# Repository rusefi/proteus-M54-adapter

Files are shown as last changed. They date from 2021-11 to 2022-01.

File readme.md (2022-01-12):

Proteus adapter for e46 non-M3 BMW

(E39 m54 should be the ms42/43 like the e46, E39 ~= E46)

https://github.com/rusefi/rusefi/wiki/BMW-e46

134 pin + Nissan board outline

https://raw.githubusercontent.com/wiki/rusefi/rusefi/OEM-Docs/Bmw/3_Series_e46/2002_bmw_325_ecu.png

https://docs.google.com/spreadsheets/d/16_VjNrk-DbMP_yDqGFelwavrGfiC9wFp73RgForjQzM

x

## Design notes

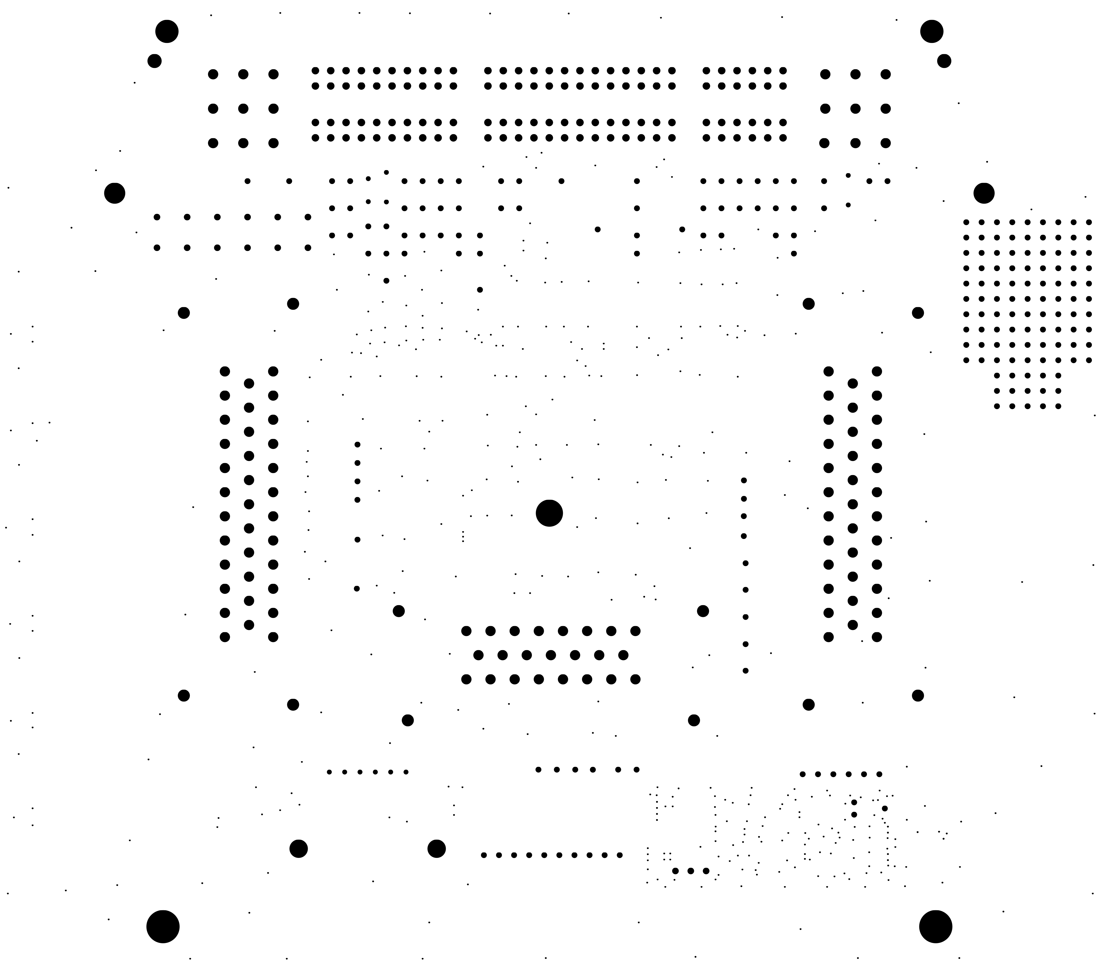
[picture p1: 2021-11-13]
proteusM54/boards/proteusM54-a/board/misc/proteusM54-a-outline.png

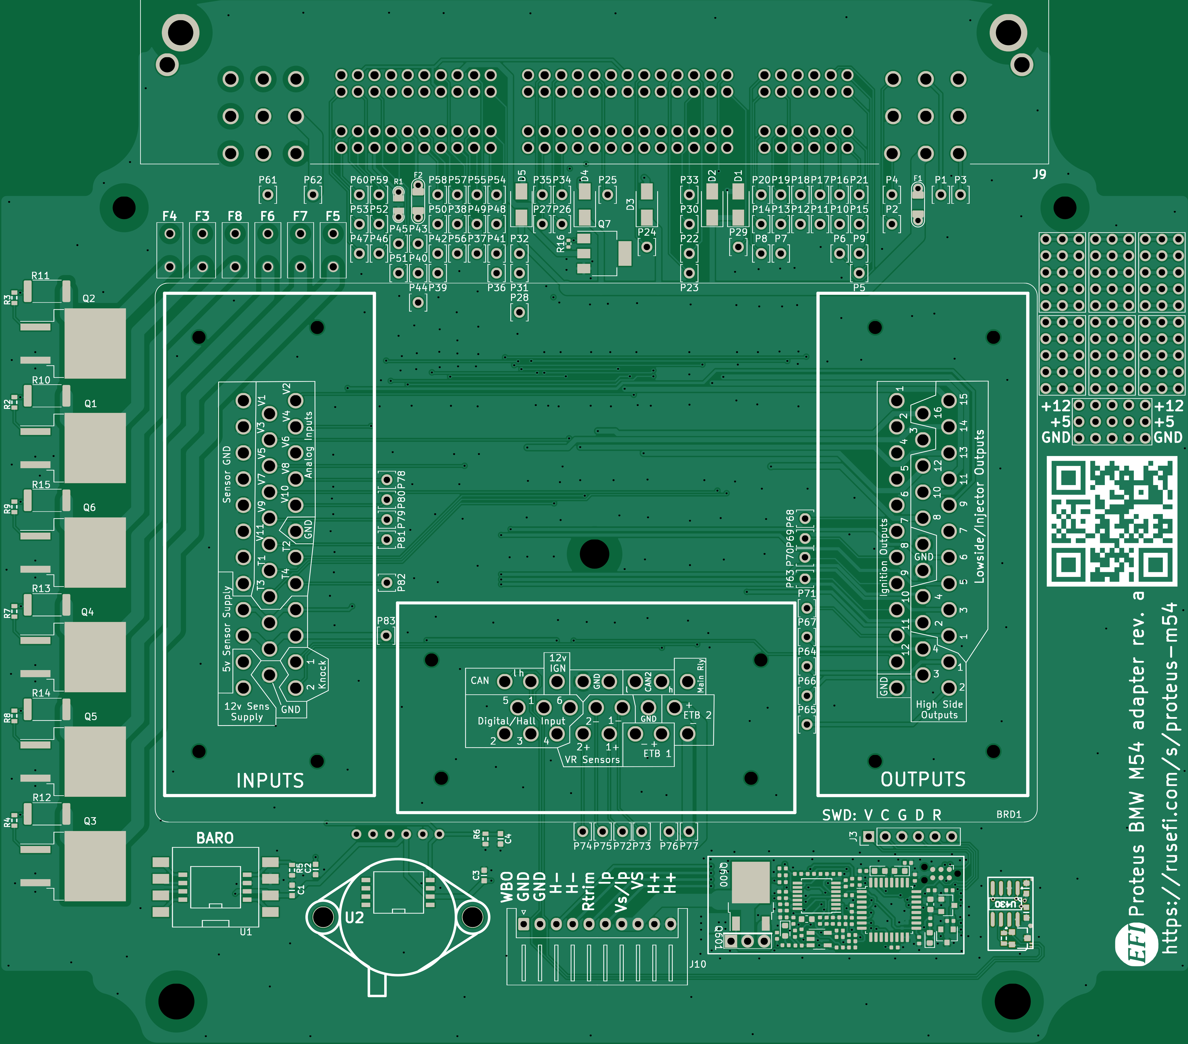
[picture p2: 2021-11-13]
proteusM54/boards/proteusM54-a/board/misc/proteusM54-a-top.png

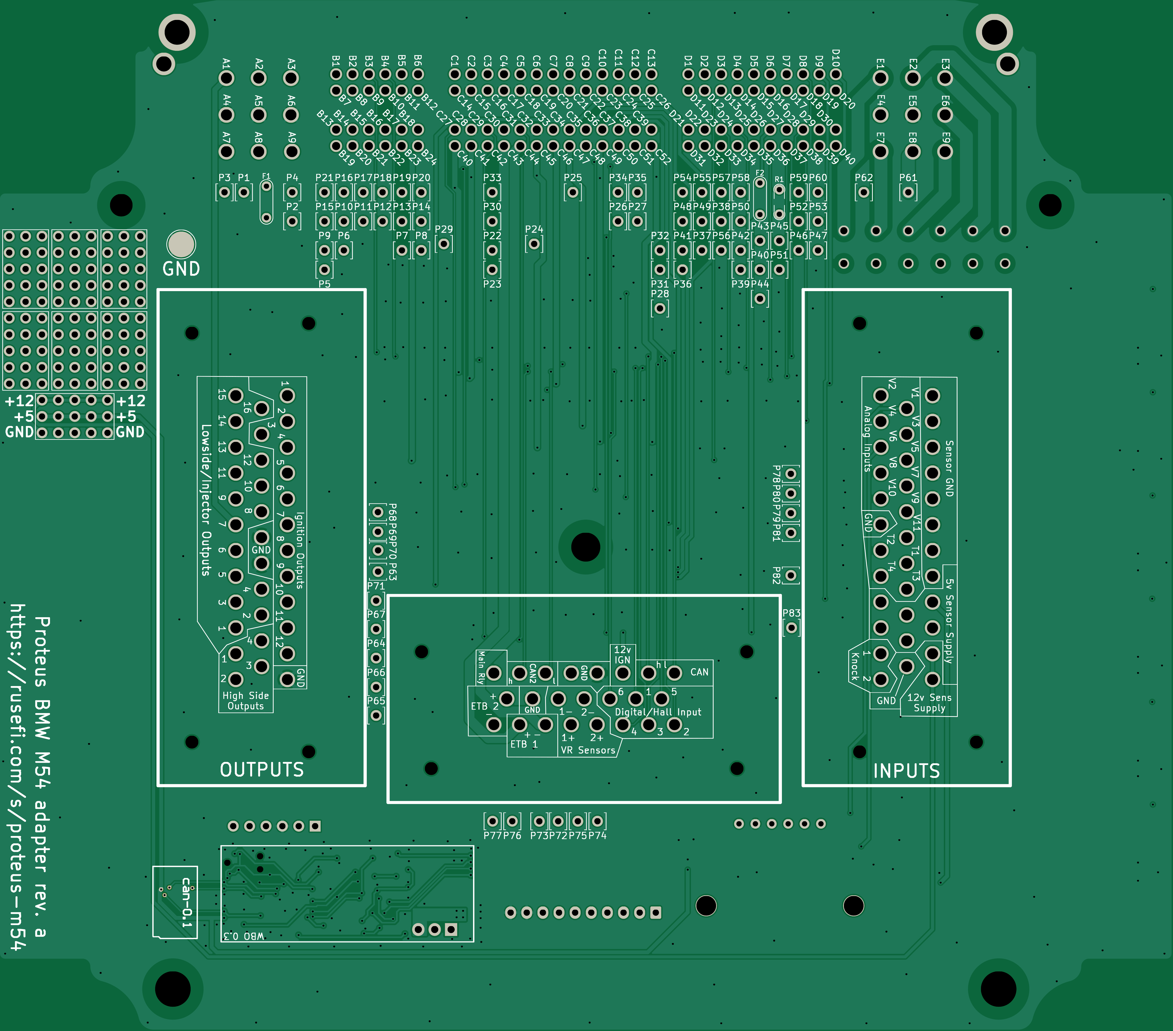
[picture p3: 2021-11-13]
proteusM54/boards/proteusM54-a/board/misc/proteusM54-a-bottom.png

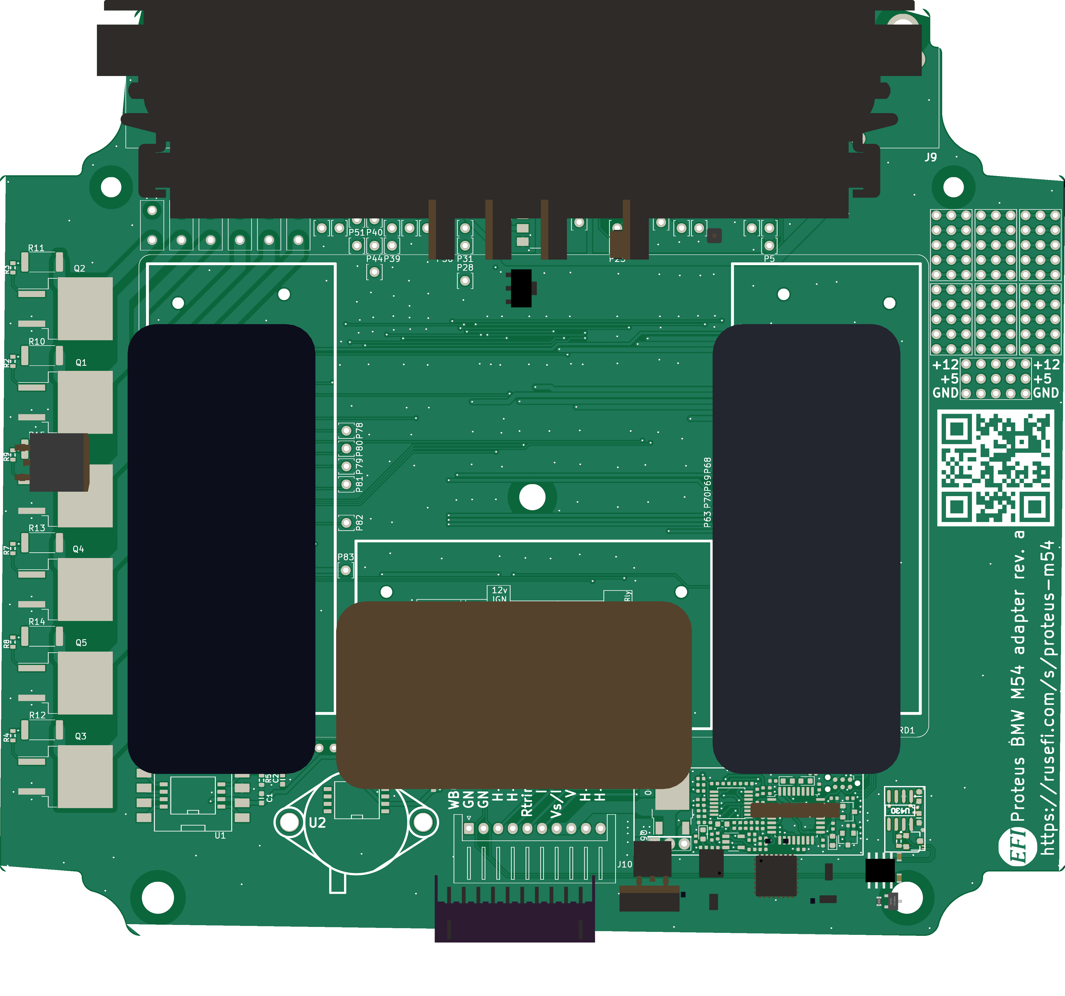
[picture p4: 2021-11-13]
proteusM54/boards/proteusM54-a/board/proteusM54-a.png

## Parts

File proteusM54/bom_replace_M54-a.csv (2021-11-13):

#WBO low-side (D2PAK | TO220)
Q600
Q601
#WBO STM32
U602
#IGN IGBT
Q1
Q2
Q3
Q4
Q5
Q6
#3.3 reference
U603 | REF3333AIDBZR | SOT-23 | C130016
#low-side
Q7 | BSP78 | SOT-223 | C56914

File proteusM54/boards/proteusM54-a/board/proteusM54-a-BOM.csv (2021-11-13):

Comment | Designator | Footprint | LCSC Part #
proteus | BRD1 | proteus
100n | C1, C3, C430, C431 | C0603 | C14663
47p | C2, C4 | C0603 | C1671
D_Schottky | D1, D2, D3, D4, D5 | D_SMA | C8678
Fuse-Pad-Pad | F1, F2 | PAD-1206-PAD | C182446
10A | F3, F4, F5, F6, F7, F8 | 36911600000 | C354908
RUSEFI_LOGO | G1 | rusefi_logo
PROTO_AREA | G2 | PROTO_AREA
PROTO_AREA | G3 | PROTO_AREA
PROTO_AREA | G4 | PROTO_AREA
PROTO_AREA | G5 | PROTO_AREA
PROTO_AREA | G6 | PROTO_AREA
PROTO_AREA | G7 | PROTO_AREA
PROTO_AREA | G8 | PROTO_AREA
Conn_01x01 | J1 | MountingHole_3.5mm
Conn_01x01 | J2 | MountingHole_3.5mm
Conn_01x06 | J3 | PinHeader_1x06_P2.54mm_Vertical
Conn_01x01 | J4 | MountingHole_5.5mm
Conn_01x01 | J5 | MountingHole_5.5mm
Conn_01x01 | J7 | TestPoint_Pad_D4.0mm
7-967288-1 | J9 | TE_7-967288-1
XH-10AW | J10 | JST_XH_S10B-XH-A_1x10_P2.50mm_Horizontal | C14652
Pad | P1 | PAD-TH
Pad | P2 | PAD-TH
Pad | P3 | PAD-TH
Pad | P4 | PAD-TH
Pad | P5 | PAD-TH
Pad | P6 | PAD-TH
Pad | P7 | PAD-TH
Pad | P8 | PAD-TH
Pad | P9 | PAD-TH
Pad | P10 | PAD-TH
Pad | P11 | PAD-TH
Pad | P12 | PAD-TH
Pad | P13 | PAD-TH
Pad | P14 | PAD-TH
Pad | P15 | PAD-TH
Pad | P16 | PAD-TH
Pad | P17 | PAD-TH
Pad | P18 | PAD-TH
Pad | P19 | PAD-TH
Pad | P20 | PAD-TH
Pad | P21 | PAD-TH
Pad | P22 | PAD-TH
Pad | P23 | PAD-TH
Pad | P24 | PAD-TH
Pad | P25 | PAD-TH
Pad | P26 | PAD-TH
Pad | P27 | PAD-TH
Pad | P28 | PAD-TH
Pad | P29 | PAD-TH
Pad | P30 | PAD-TH
Pad | P31 | PAD-TH
Pad | P32 | PAD-TH
Pad | P33 | PAD-TH
Pad | P34 | PAD-TH
Pad | P35 | PAD-TH
Pad | P36 | PAD-TH
Pad | P37 | PAD-TH
Pad | P38 | PAD-TH
Pad | P39 | PAD-TH
Pad | P40 | PAD-TH
Pad | P41 | PAD-TH
Pad | P42 | PAD-TH
Pad | P43 | PAD-TH
Pad | P44 | PAD-TH
Pad | P45 | PAD-TH
Pad | P46 | PAD-TH
Pad | P47 | PAD-TH
Pad | P48 | PAD-TH
Pad | P49 | PAD-TH
Pad | P50 | PAD-TH
Pad | P51 | PAD-TH
Pad | P52 | PAD-TH
Pad | P53 | PAD-TH
Pad | P54 | PAD-TH
Pad | P55 | PAD-TH
Pad | P56 | PAD-TH
Pad | P57 | PAD-TH
Pad | P58 | PAD-TH
Pad | P59 | PAD-TH
Pad | P60 | PAD-TH
Pad | P61 | PAD-TH
Pad | P62 | PAD-TH
Pad | P63 | PAD-TH
Pad | P64 | PAD-TH
Pad | P65 | PAD-TH
Pad | P66 | PAD-TH
Pad | P67 | PAD-TH
Pad | P68 | PAD-TH
Pad | P69 | PAD-TH
Pad | P70 | PAD-TH
Pad | P71 | PAD-TH
Pad | P72 | PAD-TH
Pad | P73 | PAD-TH
Pad | P74 | PAD-TH
Pad | P75 | PAD-TH
Pad | P76 | PAD-TH
Pad | P77 | PAD-TH
Pad | P78 | PAD-TH
Pad | P79 | PAD-TH
Pad | P80 | PAD-TH
Pad | P81 | PAD-TH
Pad | P82 | PAD-TH
Pad | P83 | PAD-TH
Jumper-Pad-Pad | R1 | PAD-0805-PAD | C17477
22 | R2, R3, R4, R7, R8, R9 | R0603 | C23345
51k | R5, R6 | R0603 | C23196
DNP | R10 | R_2512_6332Metric
DNP | R11 | R_2512_6332Metric
DNP | R12 | R_2512_6332Metric
DNP | R13 | R_2512_6332Metric
DNP | R14 | R_2512_6332Metric
DNP | R15 | R_2512_6332Metric
10k | R16 | R0402 | C60489
MPXxx6115A | U1 | MPX_SOP_SSOP
MPX4/MPXH6400_MAP | U2 | MPX-4_MAP
PESD1CAN | D430 | SOT-23 | C343993
120 | R430 | R0603 | C22787
TJA1051T/3/1J | U430 | SO8 | C38695
1u | C600, C607, C609, C610, C611 | C0402 | C52923
100n | C601, C602, C605, C608, C612, C613, C614, C615 | C0402 | C1525
33n | C603 | C0402 | C1585
DNP | C604 | C0402
DNP | C606 | C0402
4.7u | C616 | C0603 | C19666
LED-RED-0603 | D600, D603 | LED-0603 | C2286
LED-GREEN-0603 | D601 | LED-0603 | C72043
LED-BLUE-0603 | D602 | LED-0603 | C72041
1k | R600, R601, R616, R617, R622, R626, R627, R628 | R0402 | C11702
68k | R602, R603 | R0402 | C36871
10k | R604, R605, R613, R614, R618, R619, R625 | R0402 | C25744
10 | R606 | R0402 | C25077
22k | R607 | R0402 | C25768
47 | R608 | R0402 | C25118
61.9 | R609 | R0603 | C23092
20k | R610, R611, R612 | R0402 | C25765
100k | R615, R621 | R0402 | C25741
27k | R620, R623 | R0402 | C25771
3.3k | R624 | R0402 | C25890
MCP6004 | U600 | TSSOP14 | C50282
AD8628 | U601 | TSOT23-5 | C29309
XC6206P332MR | U604 | SOT-23 | C5446
REF3333AIDBZR | U603 | SOT-23 | C130016
BSP78 | Q7 | SOT-223 | C56914

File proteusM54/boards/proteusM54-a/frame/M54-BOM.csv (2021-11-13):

Comment | Designator | Footprint | LCSC Part #
proteus | BRD1 | proteus
100n | C1 | C0603 | C14663
47p | C2 | C0603 | C1671
100n | C3 | C0603 | C14663
47p | C4 | C0603 | C1671
D_Schottky | D1 | D_SMA | C8678
D_Schottky | D2 | D_SMA | C8678
D_Schottky | D3 | D_SMA | C8678
D_Schottky | D4 | D_SMA | C8678
D_Schottky | D5 | D_SMA | C8678
Fuse-Pad-Pad | F1 | PAD-1206-PAD | C182446
Fuse-Pad-Pad | F2 | PAD-1206-PAD | C182446
10A | F3 | 36911600000 | C354908
10A | F4 | 36911600000 | C354908
10A | F5 | 36911600000 | C354908
10A | F6 | 36911600000 | C354908
10A | F7 | 36911600000 | C354908
10A | F8 | 36911600000 | C354908
RUSEFI_LOGO | G1 | rusefi_logo
PROTO_AREA | G2 | PROTO_AREA
PROTO_AREA | G3 | PROTO_AREA
PROTO_AREA | G4 | PROTO_AREA
PROTO_AREA | G5 | PROTO_AREA
PROTO_AREA | G6 | PROTO_AREA
PROTO_AREA | G7 | PROTO_AREA
PROTO_AREA | G8 | PROTO_AREA
Conn_01x01 | J1 | MountingHole_3.5mm
Conn_01x01 | J2 | MountingHole_3.5mm
Conn_01x06 | J3 | PinHeader_1x06_P2.54mm_Vertical
Conn_01x01 | J4 | MountingHole_5.5mm
Conn_01x01 | J5 | MountingHole_5.5mm
Conn_01x01 | J7 | TestPoint_Pad_D4.0mm
7-967288-1 | J9 | TE_7-967288-1
XH-10AW | J10 | JST_XH_S10B-XH-A_1x10_P2.50mm_Horizontal | C14652
Module:can/0.1 | M2 | can
Module:wbo/0.3 | M3 | wbo
Pad | P1 | PAD-TH
Pad | P2 | PAD-TH
Pad | P3 | PAD-TH
Pad | P4 | PAD-TH
Pad | P5 | PAD-TH
Pad | P6 | PAD-TH
Pad | P7 | PAD-TH
Pad | P8 | PAD-TH
Pad | P9 | PAD-TH
Pad | P10 | PAD-TH
Pad | P11 | PAD-TH
Pad | P12 | PAD-TH
Pad | P13 | PAD-TH
Pad | P14 | PAD-TH
Pad | P15 | PAD-TH
Pad | P16 | PAD-TH
Pad | P17 | PAD-TH
Pad | P18 | PAD-TH
Pad | P19 | PAD-TH
Pad | P20 | PAD-TH
Pad | P21 | PAD-TH
Pad | P22 | PAD-TH
Pad | P23 | PAD-TH
Pad | P24 | PAD-TH
Pad | P25 | PAD-TH
Pad | P26 | PAD-TH
Pad | P27 | PAD-TH
Pad | P28 | PAD-TH
Pad | P29 | PAD-TH
Pad | P30 | PAD-TH
Pad | P31 | PAD-TH
Pad | P32 | PAD-TH
Pad | P33 | PAD-TH
Pad | P34 | PAD-TH
Pad | P35 | PAD-TH
Pad | P36 | PAD-TH
Pad | P37 | PAD-TH
Pad | P38 | PAD-TH
Pad | P39 | PAD-TH
Pad | P40 | PAD-TH
Pad | P41 | PAD-TH
Pad | P42 | PAD-TH
Pad | P43 | PAD-TH
Pad | P44 | PAD-TH
Pad | P45 | PAD-TH
Pad | P46 | PAD-TH
Pad | P47 | PAD-TH
Pad | P48 | PAD-TH
Pad | P49 | PAD-TH
Pad | P50 | PAD-TH
Pad | P51 | PAD-TH
Pad | P52 | PAD-TH
Pad | P53 | PAD-TH
Pad | P54 | PAD-TH
Pad | P55 | PAD-TH
Pad | P56 | PAD-TH
Pad | P57 | PAD-TH
Pad | P58 | PAD-TH
Pad | P59 | PAD-TH
Pad | P60 | PAD-TH
Pad | P61 | PAD-TH
Pad | P62 | PAD-TH
Pad | P63 | PAD-TH
Pad | P64 | PAD-TH
Pad | P65 | PAD-TH
Pad | P66 | PAD-TH
Pad | P67 | PAD-TH
Pad | P68 | PAD-TH
Pad | P69 | PAD-TH
Pad | P70 | PAD-TH
Pad | P71 | PAD-TH
Pad | P72 | PAD-TH
Pad | P73 | PAD-TH
Pad | P74 | PAD-TH
Pad | P75 | PAD-TH
Pad | P76 | PAD-TH
Pad | P77 | PAD-TH
Pad | P78 | PAD-TH
Pad | P79 | PAD-TH
Pad | P80 | PAD-TH
Pad | P81 | PAD-TH
Pad | P82 | PAD-TH
Pad | P83 | PAD-TH
ISL9V3040S3S | Q1 | TO-263-2 | C898702
ISL9V3040S3S | Q2 | TO-263-2 | C898702
ISL9V3040S3S | Q3 | TO-263-2 | C898702
ISL9V3040S3S | Q4 | TO-263-2 | C898702
ISL9V3040S3S | Q5 | TO-263-2 | C898702
ISL9V3040S3S | Q6 | TO-263-2 | C898702
AUIPS2041LTR | Q7 | SOT-223 | C113610
Jumper-Pad-Pad | R1 | PAD-0805-PAD | C17477
22 | R2 | R0603 | C23345
22 | R3 | R0603 | C23345
22 | R4 | R0603 | C23345
51k | R5 | R0603 | C23196
51k | R6 | R0603 | C23196
22 | R7 | R0603 | C23345
22 | R8 | R0603 | C23345
22 | R9 | R0603 | C23345
DNP | R10 | R_2512_6332Metric
DNP | R11 | R_2512_6332Metric
DNP | R12 | R_2512_6332Metric
DNP | R13 | R_2512_6332Metric
DNP | R14 | R_2512_6332Metric
DNP | R15 | R_2512_6332Metric
10k | R16 | R0402 | C60489
MPXxx6115A | U1 | MPX_SOP_SSOP
MPX4/MPXH6400_MAP | U2 | MPX-4_MAP

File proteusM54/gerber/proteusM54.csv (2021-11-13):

Comment | Designator | Footprint | LCSC Part #
proteus | BRD1 | kicad6-libraries:proteus
100n | C1 | hellen-one-common:C0603 | C14663
47p | C2 | hellen-one-common:C0603 | C1671
100n | C3 | hellen-one-common:C0603 | C14663
47p | C4 | hellen-one-common:C0603 | C1671
D_Schottky | D1 | Diode_SMD:D_SMA | C8678
D_Schottky | D2 | Diode_SMD:D_SMA | C8678
D_Schottky | D3 | Diode_SMD:D_SMA | C8678
D_Schottky | D4 | Diode_SMD:D_SMA | C8678
D_Schottky | D5 | Diode_SMD:D_SMA | C8678
Fuse-Pad-Pad | F1 | hellen-one-common:PAD-1206-PAD | C182446
Fuse-Pad-Pad | F2 | hellen-one-common:PAD-1206-PAD | C182446
10A | F3 | hellen-one-common:36911600000 | C354908
10A | F4 | hellen-one-common:36911600000 | C354908
10A | F5 | hellen-one-common:36911600000 | C354908
10A | F6 | hellen-one-common:36911600000 | C354908
10A | F7 | hellen-one-common:36911600000 | C354908
10A | F8 | hellen-one-common:36911600000 | C354908
RUSEFI_LOGO | G1 | kicad6-libraries:rusefi_logo
PROTO_AREA | G2 | hellen-one-common:PROTO_AREA
PROTO_AREA | G3 | hellen-one-common:PROTO_AREA
PROTO_AREA | G4 | hellen-one-common:PROTO_AREA
PROTO_AREA | G5 | hellen-one-common:PROTO_AREA
PROTO_AREA | G6 | hellen-one-common:PROTO_AREA
PROTO_AREA | G7 | hellen-one-common:PROTO_AREA
PROTO_AREA | G8 | hellen-one-common:PROTO_AREA
Conn_01x01 | J1 | MountingHole:MountingHole_3.5mm
Conn_01x01 | J2 | MountingHole:MountingHole_3.5mm
Conn_01x06 | J3 | Connector_PinHeader_2.54mm:PinHeader_1x06_P2.54mm_Vertical
Conn_01x01 | J4 | MountingHole:MountingHole_5.5mm
Conn_01x01 | J5 | MountingHole:MountingHole_5.5mm
Conn_01x01 | J7 | TestPoint:TestPoint_Pad_D4.0mm
7-967288-1 | J9 | kicad6-libraries:TE_7-967288-1
XH-10AW | J10 | Connector_JST:JST_XH_S10B-XH-A_1x10_P2.50mm_Horizontal | C14652
Module-can-0.1 | M2 | hellen-one-can-0.1:can
Module-wbo-0.3 | M3 | hellen-one-wbo-0.3:wbo
Pad | P1 | hellen-one-common:PAD-TH
Pad | P2 | hellen-one-common:PAD-TH
Pad | P3 | hellen-one-common:PAD-TH
Pad | P4 | hellen-one-common:PAD-TH
Pad | P5 | hellen-one-common:PAD-TH
Pad | P6 | hellen-one-common:PAD-TH
Pad | P7 | hellen-one-common:PAD-TH
Pad | P8 | hellen-one-common:PAD-TH
Pad | P9 | hellen-one-common:PAD-TH
Pad | P10 | hellen-one-common:PAD-TH
Pad | P11 | hellen-one-common:PAD-TH
Pad | P12 | hellen-one-common:PAD-TH
Pad | P13 | hellen-one-common:PAD-TH
Pad | P14 | hellen-one-common:PAD-TH
Pad | P15 | hellen-one-common:PAD-TH
Pad | P16 | hellen-one-common:PAD-TH
Pad | P17 | hellen-one-common:PAD-TH
Pad | P18 | hellen-one-common:PAD-TH
Pad | P19 | hellen-one-common:PAD-TH
Pad | P20 | hellen-one-common:PAD-TH
Pad | P21 | hellen-one-common:PAD-TH
Pad | P22 | hellen-one-common:PAD-TH
Pad | P23 | hellen-one-common:PAD-TH
Pad | P24 | hellen-one-common:PAD-TH
Pad | P25 | hellen-one-common:PAD-TH
Pad | P26 | hellen-one-common:PAD-TH
Pad | P27 | hellen-one-common:PAD-TH
Pad | P28 | hellen-one-common:PAD-TH
Pad | P29 | hellen-one-common:PAD-TH
Pad | P30 | hellen-one-common:PAD-TH
Pad | P31 | hellen-one-common:PAD-TH
Pad | P32 | hellen-one-common:PAD-TH
Pad | P33 | hellen-one-common:PAD-TH
Pad | P34 | hellen-one-common:PAD-TH
Pad | P35 | hellen-one-common:PAD-TH
Pad | P36 | hellen-one-common:PAD-TH
Pad | P37 | hellen-one-common:PAD-TH
Pad | P38 | hellen-one-common:PAD-TH
Pad | P39 | hellen-one-common:PAD-TH
Pad | P40 | hellen-one-common:PAD-TH
Pad | P41 | hellen-one-common:PAD-TH
Pad | P42 | hellen-one-common:PAD-TH
Pad | P43 | hellen-one-common:PAD-TH
Pad | P44 | hellen-one-common:PAD-TH
Pad | P45 | hellen-one-common:PAD-TH
Pad | P46 | hellen-one-common:PAD-TH
Pad | P47 | hellen-one-common:PAD-TH
Pad | P48 | hellen-one-common:PAD-TH
Pad | P49 | hellen-one-common:PAD-TH
Pad | P50 | hellen-one-common:PAD-TH
Pad | P51 | hellen-one-common:PAD-TH
Pad | P52 | hellen-one-common:PAD-TH
Pad | P53 | hellen-one-common:PAD-TH
Pad | P54 | hellen-one-common:PAD-TH
Pad | P55 | hellen-one-common:PAD-TH
Pad | P56 | hellen-one-common:PAD-TH
Pad | P57 | hellen-one-common:PAD-TH
Pad | P58 | hellen-one-common:PAD-TH
Pad | P59 | hellen-one-common:PAD-TH
Pad | P60 | hellen-one-common:PAD-TH
Pad | P61 | hellen-one-common:PAD-TH
Pad | P62 | hellen-one-common:PAD-TH
Pad | P63 | hellen-one-common:PAD-TH
Pad | P64 | hellen-one-common:PAD-TH
Pad | P65 | hellen-one-common:PAD-TH
Pad | P66 | hellen-one-common:PAD-TH
Pad | P67 | hellen-one-common:PAD-TH
Pad | P68 | hellen-one-common:PAD-TH
Pad | P69 | hellen-one-common:PAD-TH
Pad | P70 | hellen-one-common:PAD-TH
Pad | P71 | hellen-one-common:PAD-TH
Pad | P72 | hellen-one-common:PAD-TH
Pad | P73 | hellen-one-common:PAD-TH
Pad | P74 | hellen-one-common:PAD-TH
Pad | P75 | hellen-one-common:PAD-TH
Pad | P76 | hellen-one-common:PAD-TH
Pad | P77 | hellen-one-common:PAD-TH
Pad | P78 | hellen-one-common:PAD-TH
Pad | P79 | hellen-one-common:PAD-TH
Pad | P80 | hellen-one-common:PAD-TH
Pad | P81 | hellen-one-common:PAD-TH
Pad | P82 | hellen-one-common:PAD-TH
Pad | P83 | hellen-one-common:PAD-TH
ISL9V3040S3S | Q1 | Package_TO_SOT_SMD:TO-263-2 | C898702
ISL9V3040S3S | Q2 | Package_TO_SOT_SMD:TO-263-2 | C898702
ISL9V3040S3S | Q3 | Package_TO_SOT_SMD:TO-263-2 | C898702
ISL9V3040S3S | Q4 | Package_TO_SOT_SMD:TO-263-2 | C898702
ISL9V3040S3S | Q5 | Package_TO_SOT_SMD:TO-263-2 | C898702
ISL9V3040S3S | Q6 | Package_TO_SOT_SMD:TO-263-2 | C898702
AUIPS2041LTR | Q7 | Package_TO_SOT_SMD:SOT-223 | C113610
Jumper-Pad-Pad | R1 | hellen-one-common:PAD-0805-PAD | C17477
22 | R2 | hellen-one-common:R0603 | C23345
22 | R3 | hellen-one-common:R0603 | C23345
22 | R4 | hellen-one-common:R0603 | C23345
51k | R5 | hellen-one-common:R0603 | C23196
51k | R6 | hellen-one-common:R0603 | C23196
22 | R7 | hellen-one-common:R0603 | C23345
22 | R8 | hellen-one-common:R0603 | C23345
22 | R9 | hellen-one-common:R0603 | C23345
DNP | R10 | Resistor_SMD:R_2512_6332Metric
DNP | R11 | Resistor_SMD:R_2512_6332Metric
DNP | R12 | Resistor_SMD:R_2512_6332Metric
DNP | R13 | Resistor_SMD:R_2512_6332Metric
DNP | R14 | Resistor_SMD:R_2512_6332Metric
DNP | R15 | Resistor_SMD:R_2512_6332Metric
10k | R16 | Resistor_SMD:R_0402_1005Metric | C60489
MPXxx6115A | U1 | kicad6-libraries:MPX_SOP_SSOP
MPX4/MPXH6400_MAP | U2 | kicad6-libraries:MPX-4_MAP

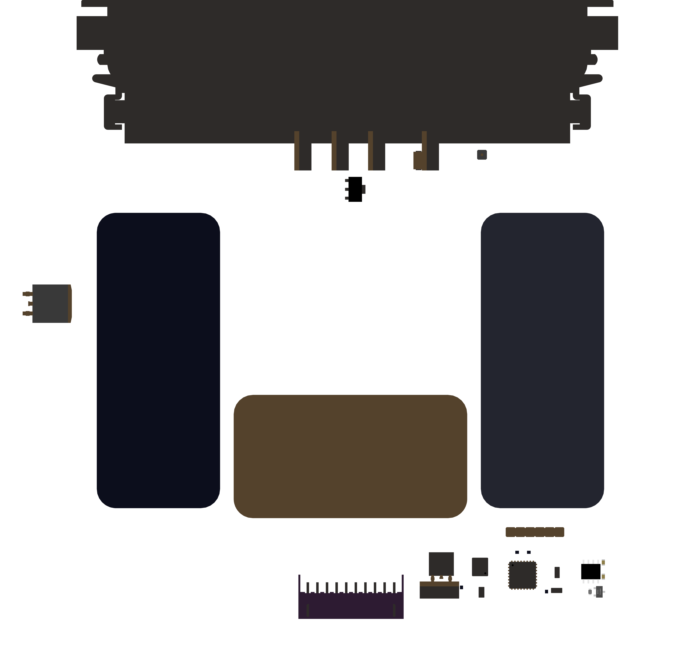
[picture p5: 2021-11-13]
proteusM54/boards/proteusM54-a/board/misc/proteusM54-a-components.png

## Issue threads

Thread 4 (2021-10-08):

Validate pinout

rusefillc, 2021-10-08:
We need to confirm that for each of the 134 pins we have connected it properly
for each pins options are

- ignore
- just a prototyping via just in case
- low side without flyback
- low side with flyback
- low current low side for relay
- low current high side
- high current high side
- analog with pull-down
- analog with pull-up
- 5v
- GND

rusefillc, 2021-10-09:
@Qwerty-OFF do you think we can have vias for all unrouted connector pins?

Qwerty-OFF, 2021-11-09:
Possibly vias for all unrouted connector pins require 4-layer board. Is it OK?
Are jumpers required for all used pins?
We don't have enough low-side pins. Can I use IGN outputs to drive MOSFETs?
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

rusefillc, 2021-11-09:
4 layers totally fine

mck1117, 2021-11-09:
>  We don't have enough low-side pins. Can I use IGN outputs to drive MOSFETs?

yes, no problem there!

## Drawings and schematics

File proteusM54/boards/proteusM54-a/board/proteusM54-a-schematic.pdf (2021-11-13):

# GND GND GND GND

P18 P16

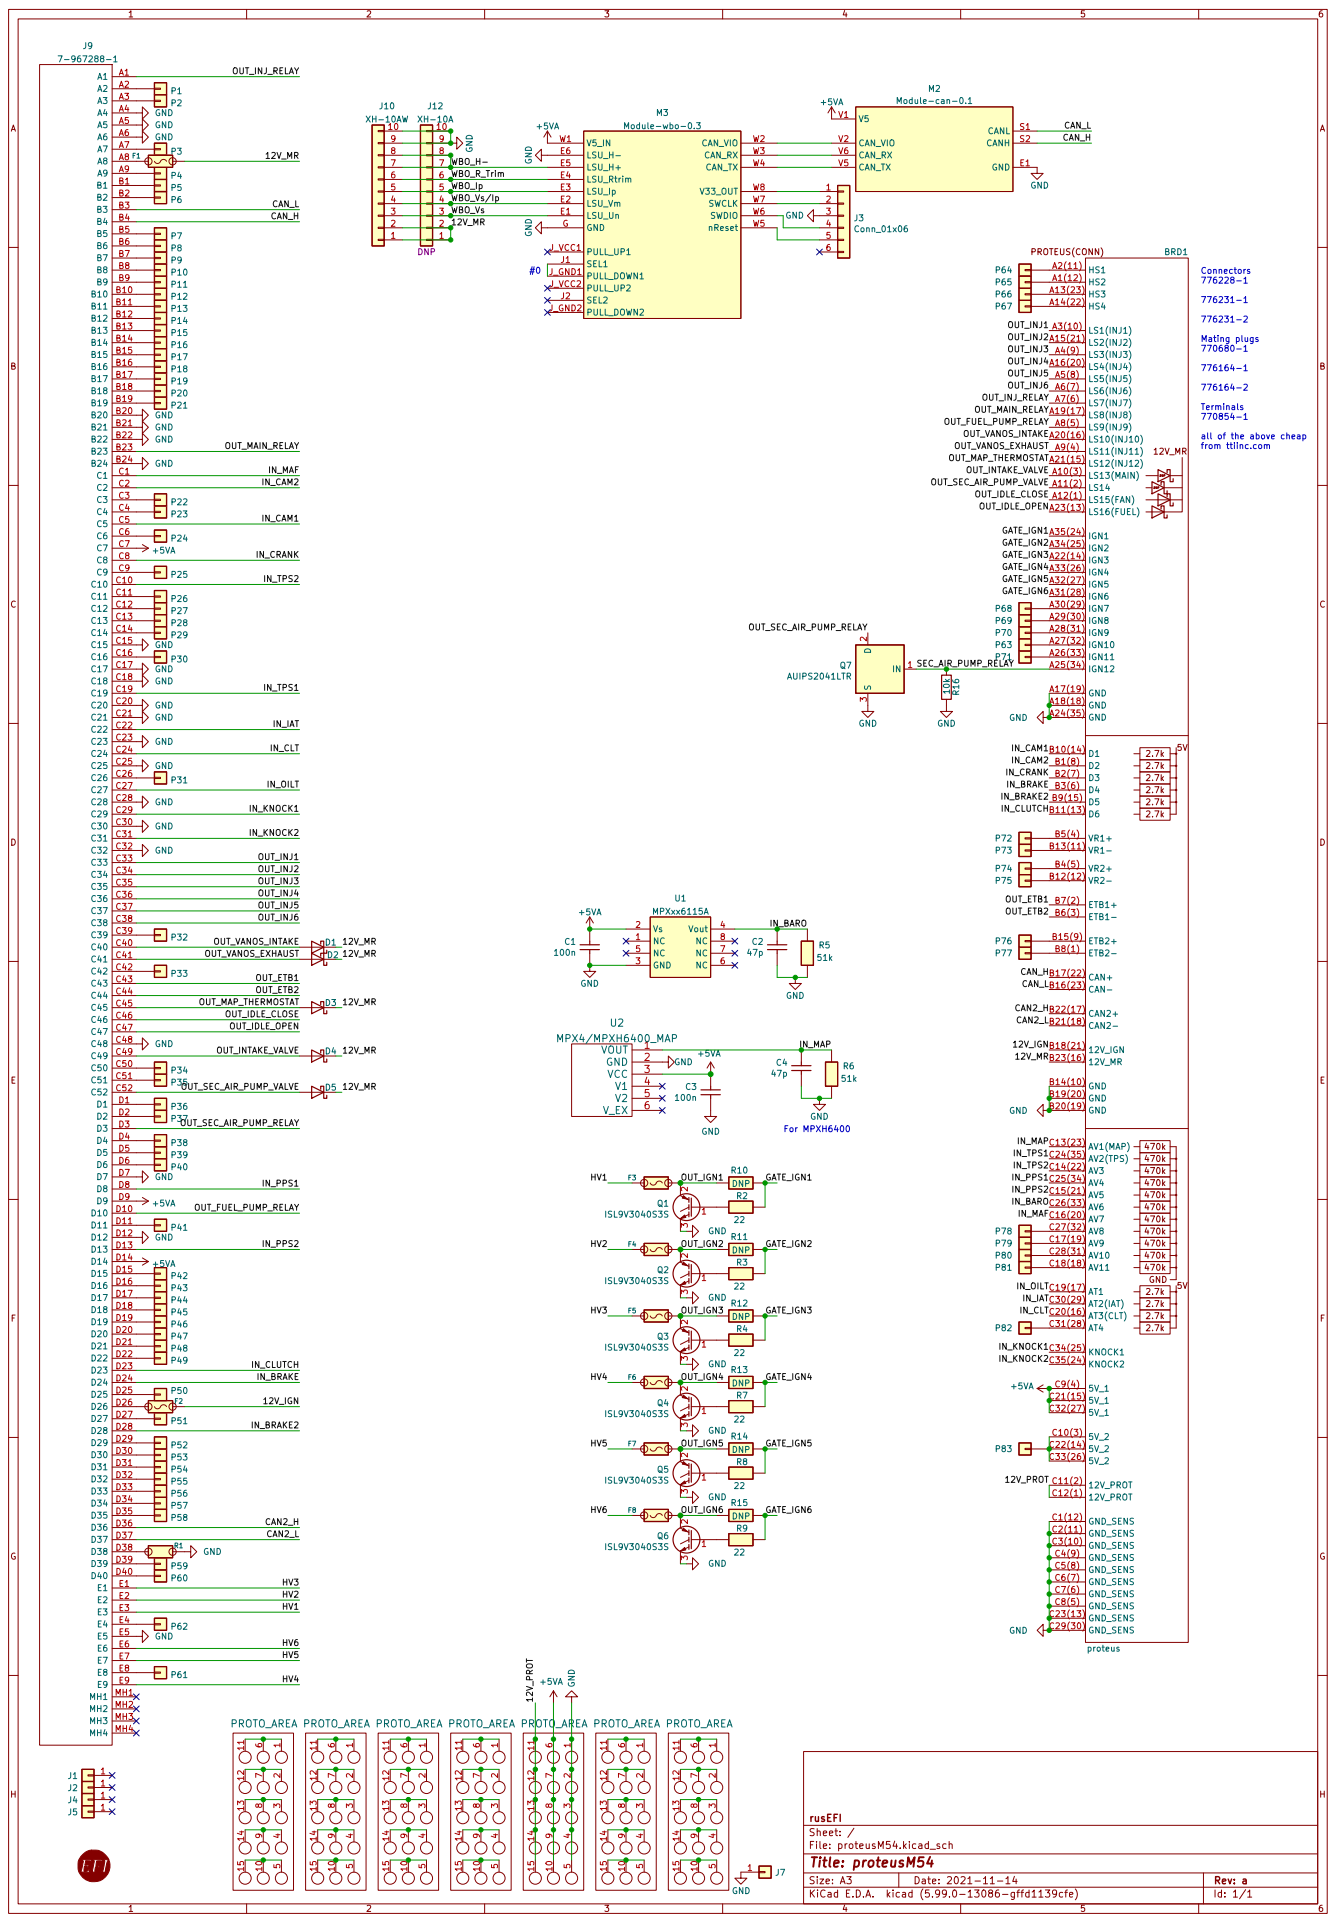
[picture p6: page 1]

all of the above cheap
from ttiinc.com

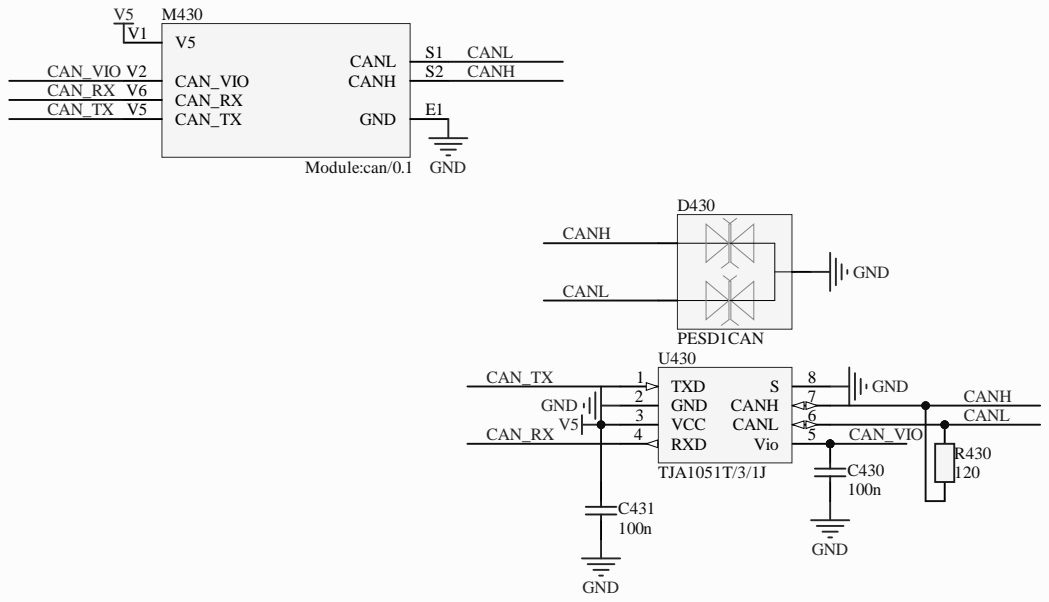
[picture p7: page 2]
andreika; Size:; Author:; Date:; Revision:; Sheet; PESD1CAN; GND; CANH; CANL; TXD 1 GND 2 VCC 3; Vio; 5 RXD 4; 6 CANH; TJA1051T/3/1J; CANH CANL; CAN_TX; CAN_RX; CAN_VIO; CAN_VIO V2; S2 CANL; CAN_TX V5; CAN_RX V6; Module:can/0.1

Hellen-One CAN
Title:

rusEFI EMS
Hellen-One Platform
https://rusefi.com/s/hellen72

1kR600

3.3k R623

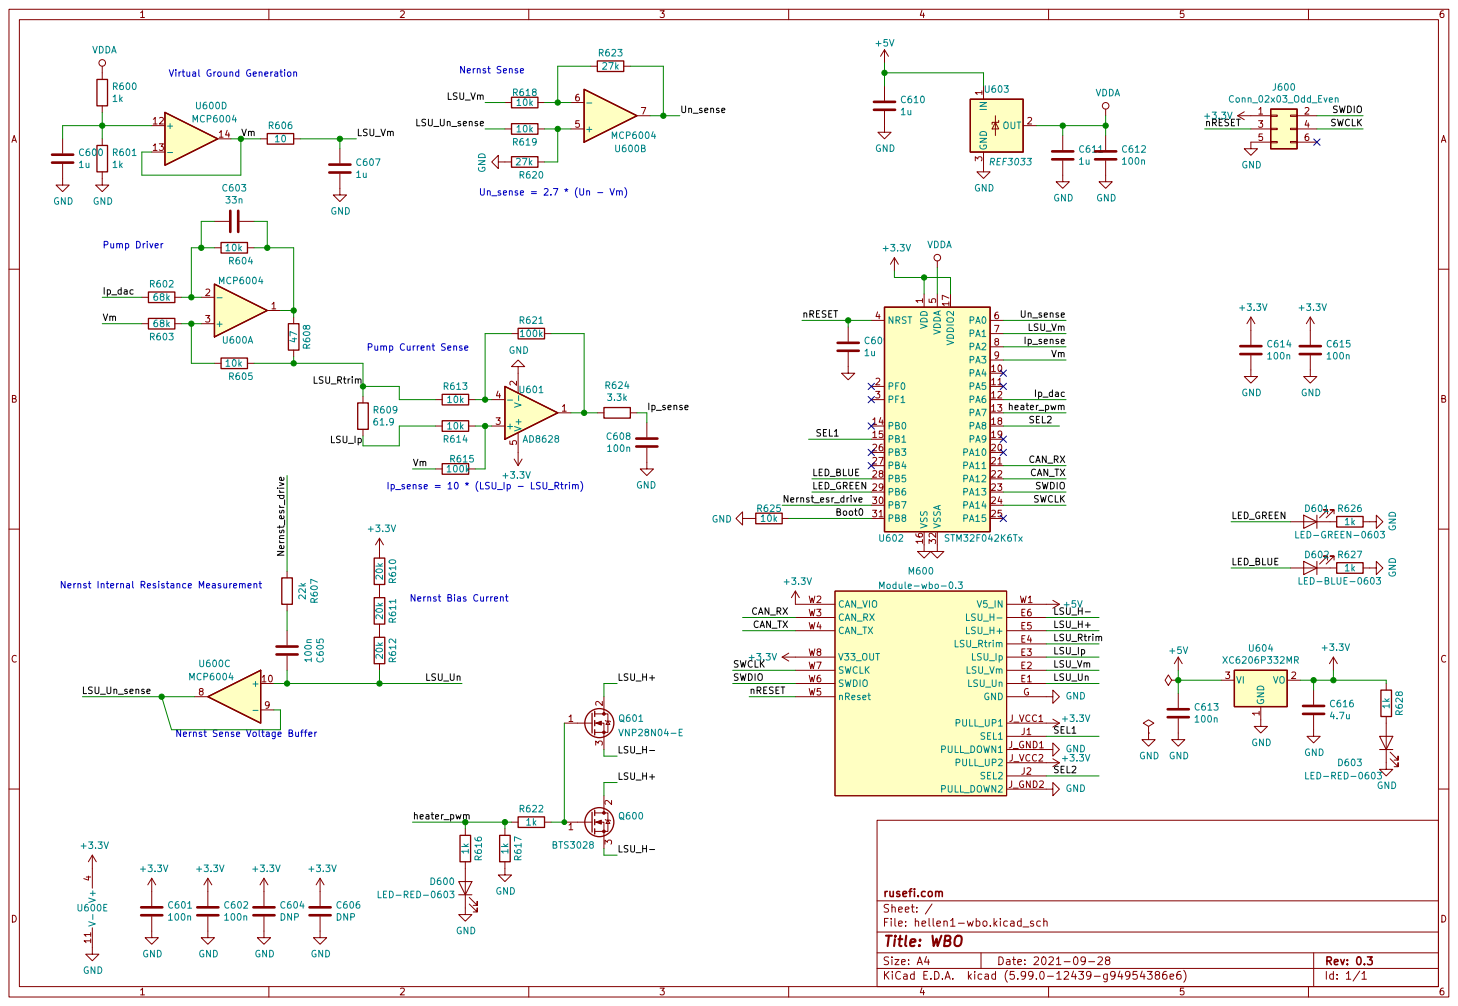
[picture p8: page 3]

Pump Current Sense Nernst Sense

LSU_Vm
Pump Driver Nernst Internal Resistance Measurement

1 VO 2 VI 3 U604 XC6206P332MR GND GND

1 PA4 10 PA5 11 PA6 12 PA7 13 PB0 14 PB1 15 VSS 16 VDDIO2 17 PA8 18 PA9 19 PF0 2 PA10 20 PA11 21 PA12 22 PA13 23 PA14 24 PA15 25 PB3 26 PB4 27 PB5 28 PB6 29 PF1 3 PB7 30 PB8 31 VSSA 32 NRST 4 VDDA

LED-RED-0603 ¹⁰⁰n C⁶⁰⁵ C604 DNP

Nernst Sense Voltage Buffer

1k GND GND R⁶¹⁶ ¹k

File: hellen1-wbo.kicad_sch Sheet: / rusefi.com

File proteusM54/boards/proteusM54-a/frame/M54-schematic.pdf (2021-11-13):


J12 XH-10A DNP GND GND GND
GND

GND GND

all of the above cheap
from ttiinc.com

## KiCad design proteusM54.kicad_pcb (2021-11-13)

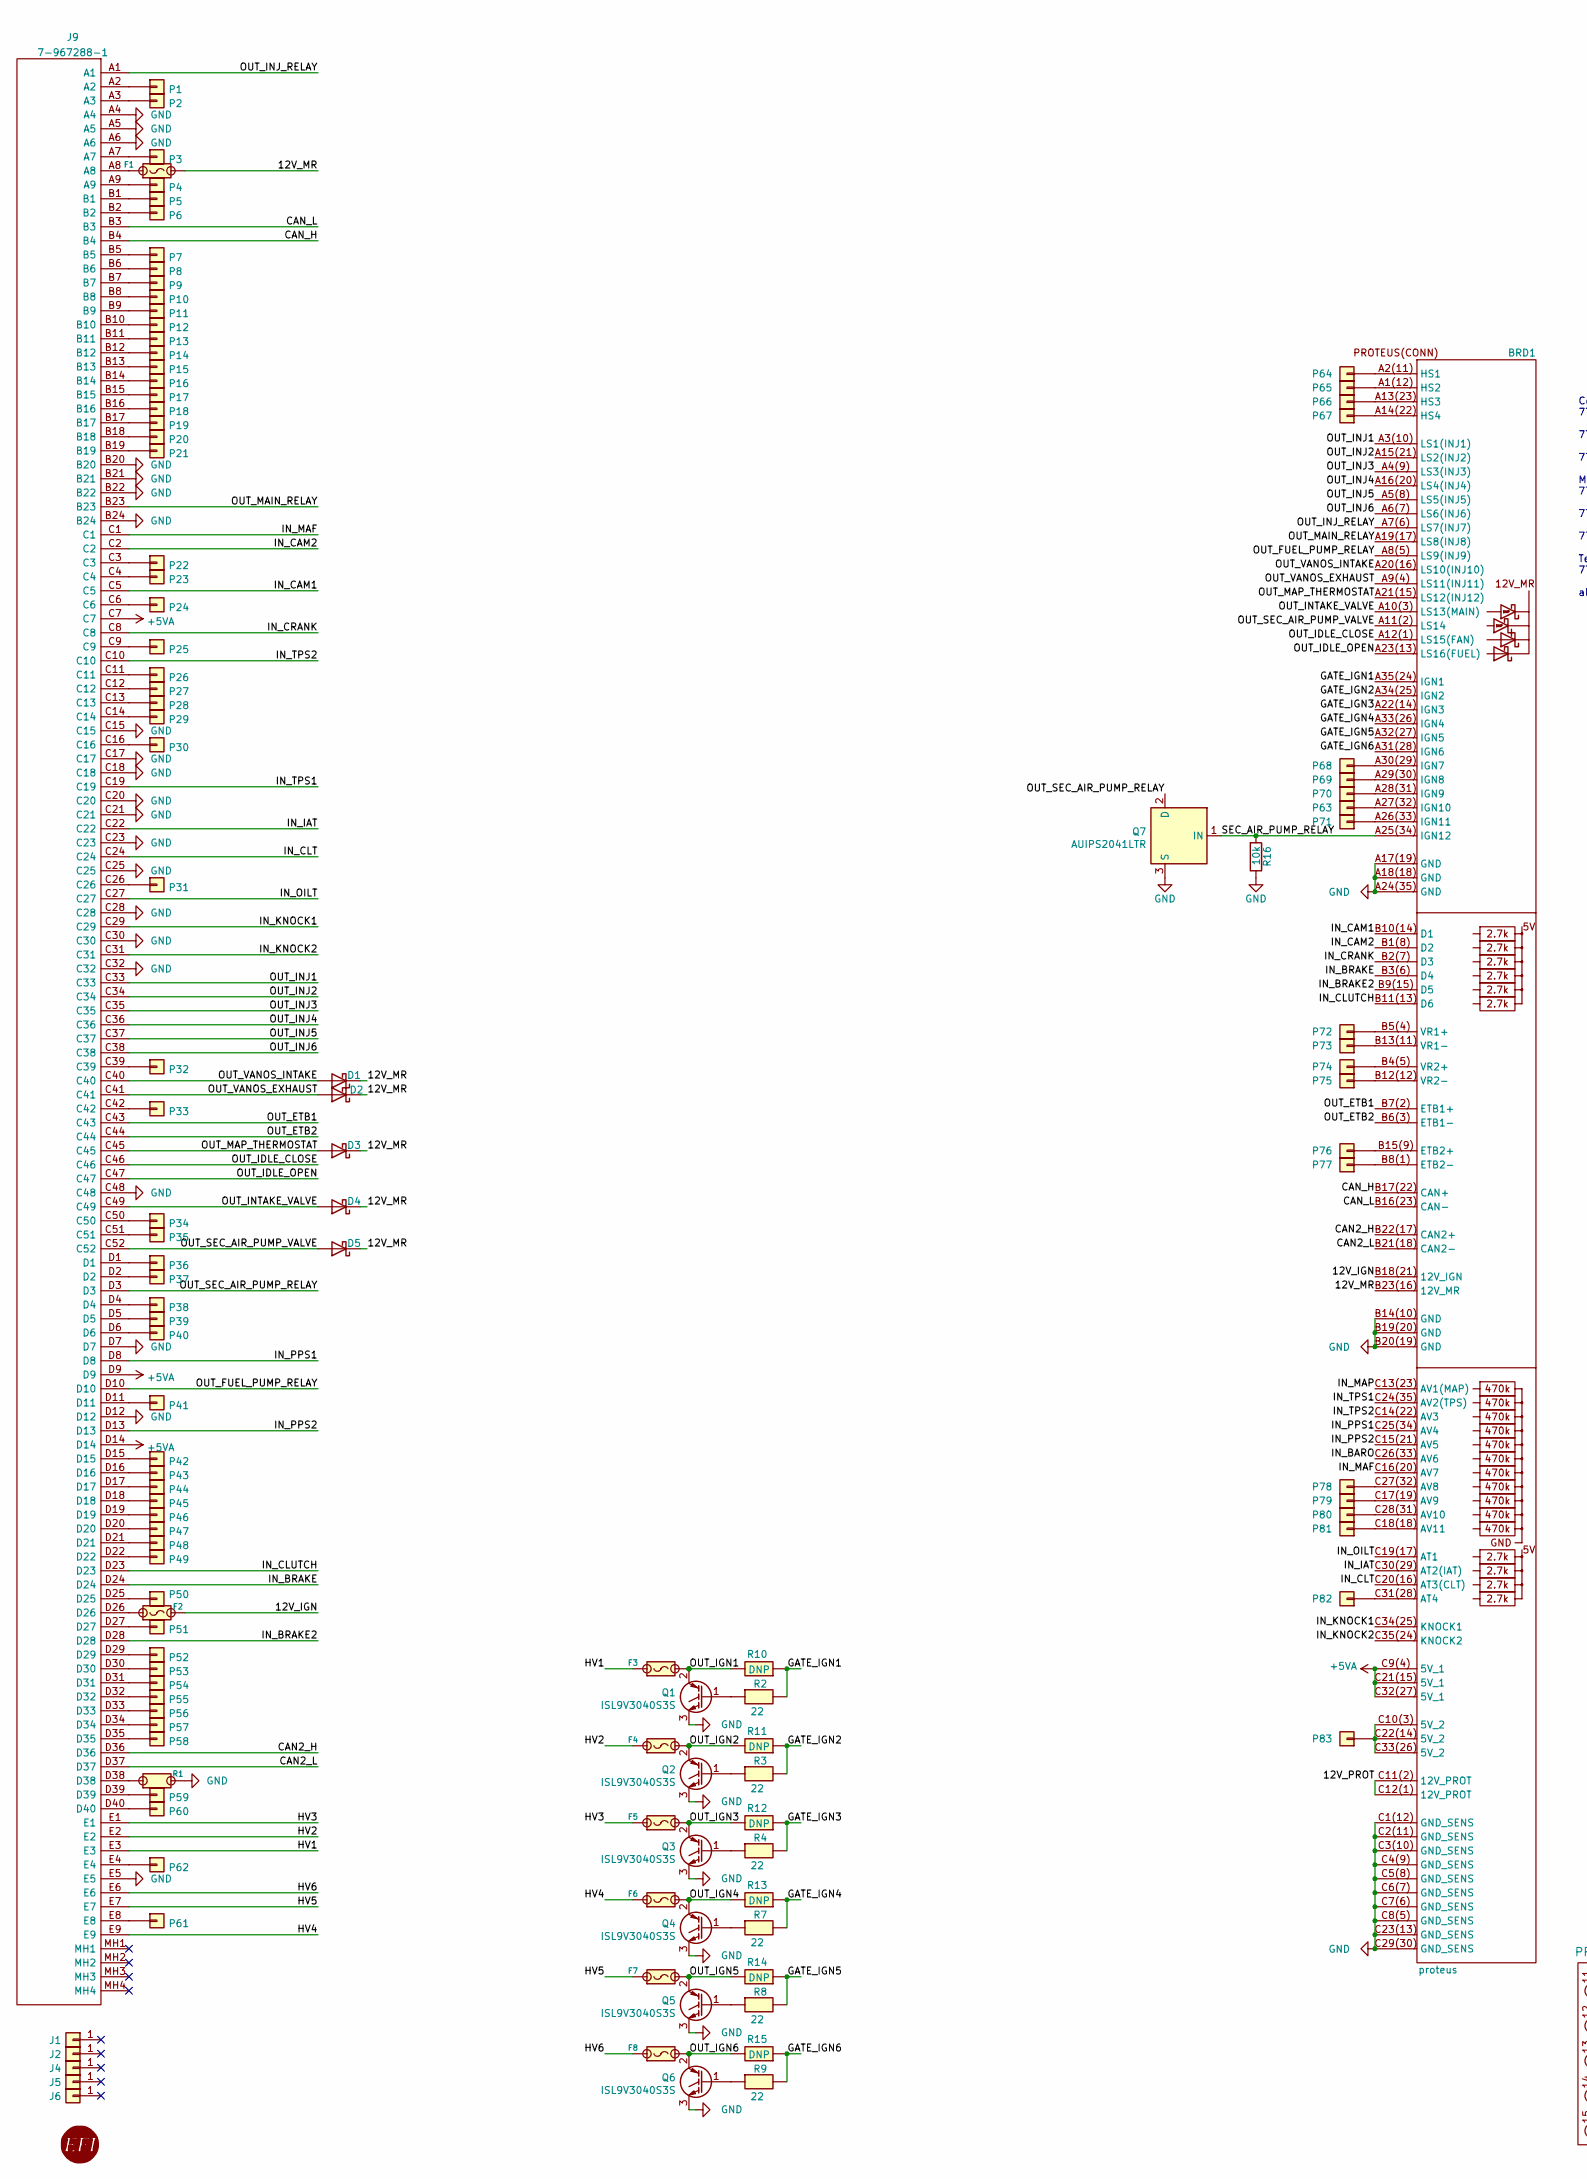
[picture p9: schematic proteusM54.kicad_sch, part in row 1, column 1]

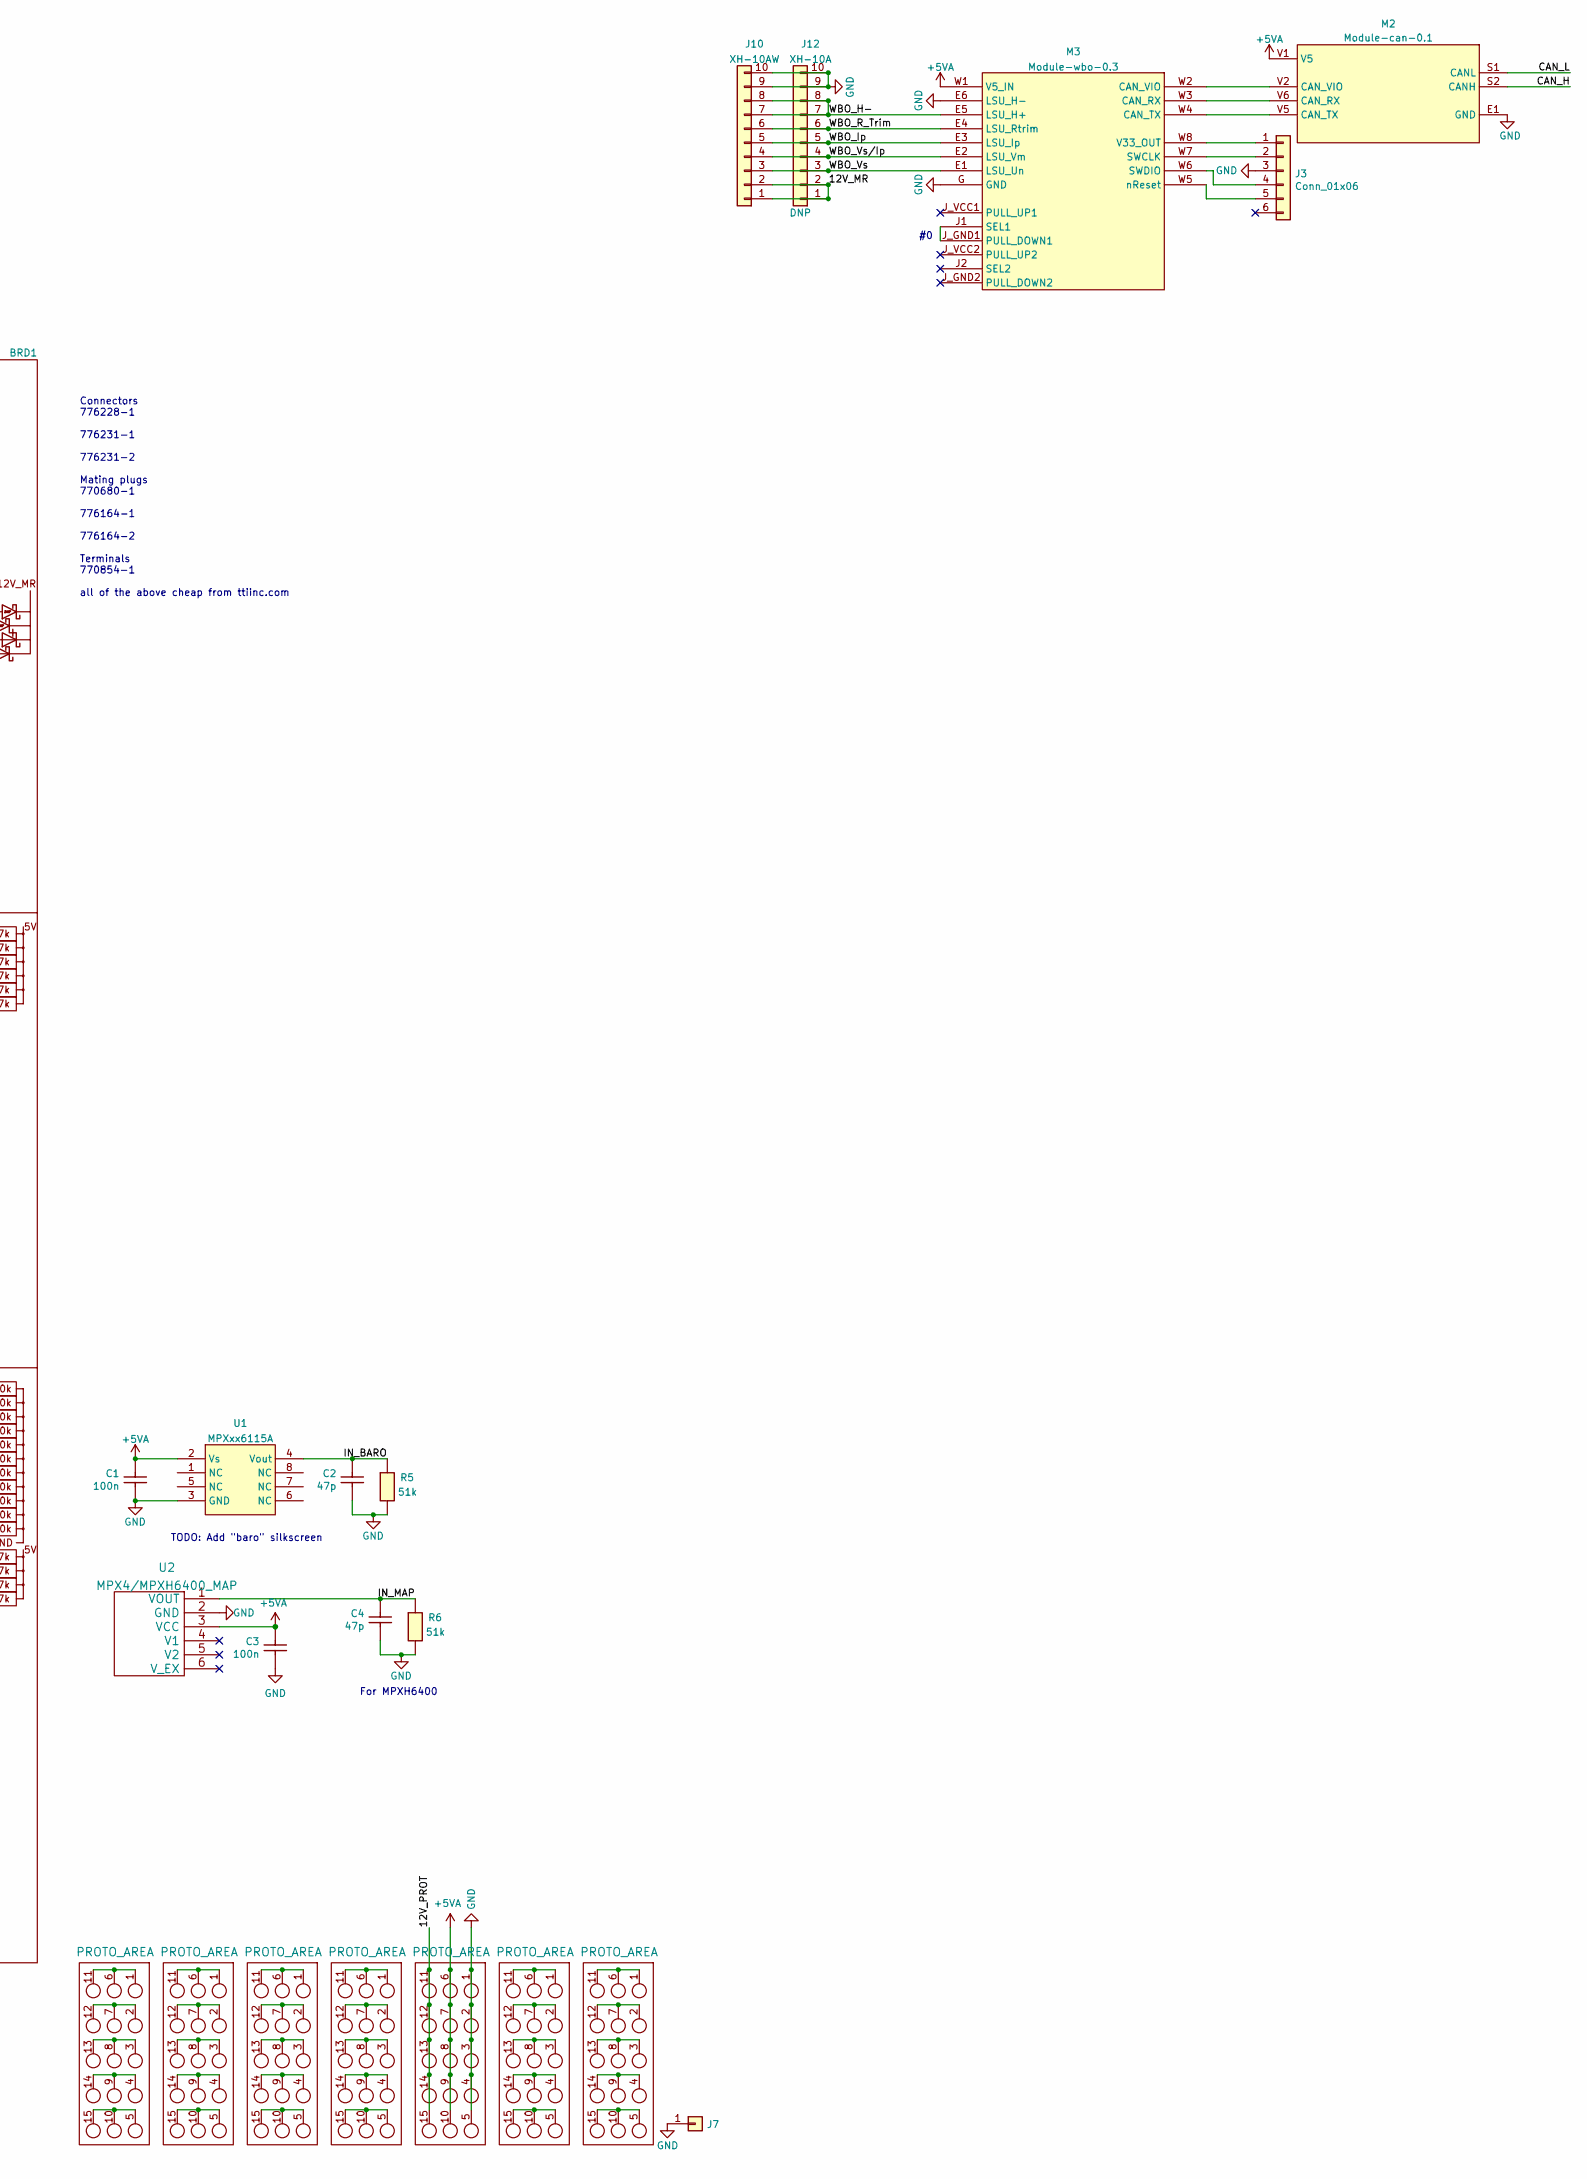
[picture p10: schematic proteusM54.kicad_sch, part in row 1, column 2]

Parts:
BRD1: proteus
C1, C3: 100n; C0603; LCSC C14663
C2, C4: 47p; C0603; LCSC C1671
D1, D2, D3, D4, D5: D_Schottky; D_SMA; LCSC C8678
F1, F2: Fuse-Pad-Pad; PAD-1206-PAD; LCSC C182446
F3, F4, F5, F6, F7, F8: 10A; 36911600000; LCSC C354908
G1: RUSEFI_LOGO; rusefi_logo
G2, G3, G4, G5, G6, G7, G8: PROTO_AREA
J1, J2: Conn_01x01; MountingHole_3.5mm
J3: Conn_01x06; PinHeader_1x06_P2.54mm_Vertical
J4, J5: Conn_01x01; MountingHole_5.5mm
J6: Conn_01x01; MountingHole_4.5mm
J7: Conn_01x01; TestPoint_Pad_D4.0mm
J9: 7-967288-1; TE_7-967288-1; Mouser Part Number 571-7-967288-1
J10: XH-10AW; JST_XH_S10B-XH-A_1x10_P2.50mm_Horizontal; LCSC C14652
J12: XH-10A; JST_XH_B10B-XH-A_1x10_P2.50mm_Vertical; LCSC C8885
M2: Module-can-0.1; can
M3: Module-wbo-0.3; wbo
P1, P2, P3, P4, P5, P6, P7, P8, P9, P10, P11, P12, P13, P14, P15, P16, P17, P18, P19, P20, P21, P22, P23, P24, P25, P26, P27, P28, P29, P30, P31, P32, P33, P34, P35, P36, P37, P38, P39, P40, P41, P42, P43, P44, P45, P46, P47, P48, P49, P50, P51, P52, P53, P54, P55, P56, P57, P58, P59, P60, P61, P62, P63, P64, P65, P66, P67, P68, P69, P70, P71, P72, P73, P74, P75, P76, P77, P78, P79, P80, P81, P82, P83: Pad; PAD-TH
Q1, Q2, Q3, Q4, Q5, Q6: ISL9V3040S3S; TO-263-2; LCSC C898702
Q7: AUIPS2041LTR; SOT-223; LCSC C113610
R1: Jumper-Pad-Pad; PAD-0805-PAD; LCSC C17477
R2, R3, R4, R7, R8, R9: 22; R0603; LCSC C23345
R5, R6: 51k; R0603; LCSC C23196
R10, R11, R12, R13, R14, R15: DNP; R_2512_6332Metric
R16: 10k; R_0402_1005Metric; LCSC C60489
U1: MPXxx6115A; MPX_SOP_SSOP
U2: MPX4/MPXH6400_MAP; MPX-4_MAP

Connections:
+5VA: BRD1.C9(4) (5V_1), BRD1.C21(15) (5V_1), BRD1.C32(27) (5V_1), C1.2, C3.2, G6.6, G6.7, G6.8, G6.9, G6.10, J9.C7, J9.D9, J9.D14, M2.V1 (V5), M3.W1 (V5_IN), U1.2 (Vs), U2.3 (VCC)
/12V_IGN: BRD1.B18(21) (12V_IGN), F2.2
/12V_MR: BRD1.B23(16) (12V_MR), D1.1 (K), D2.1 (K), D3.1 (K), D4.1 (K), D5.1 (K), F1.2, J10.1, J10.2, J12.1, J12.2
/12V_PROT: BRD1.C11(2) (12V_PROT), BRD1.C12(1) (12V_PROT), G6.11, G6.12, G6.13, G6.14, G6.15
/CAN2_H: BRD1.B22(17) (CAN2+), J9.D36
/CAN2_L: BRD1.B21(18) (CAN2-), J9.D37
/CAN_H: BRD1.B17(22) (CAN+), J9.B4, M2.S2 (CANH)
/CAN_L: BRD1.B16(23) (CAN-), J9.B3, M2.S1 (CANL)
/GATE_IGN1: BRD1.A35(24) (IGN1), R2.2, R10.1
/GATE_IGN2: BRD1.A34(25) (IGN2), R3.2, R11.1
/GATE_IGN3: BRD1.A22(14) (IGN3), R4.2, R12.1
/GATE_IGN4: BRD1.A33(26) (IGN4), R7.2, R13.1
/GATE_IGN5: BRD1.A32(27) (IGN5), R8.2, R14.1
/GATE_IGN6: BRD1.A31(28) (IGN6), R9.2, R15.1
/HV1: F3.1, J9.E3
/HV2: F4.1, J9.E2
/HV3: F5.1, J9.E1
/HV4: F6.1, J9.E9
/HV5: F7.1, J9.E7
/HV6: F8.1, J9.E6
/IN_BARO: BRD1.C26(33) (AV6), C2.2, R5.1, U1.4 (Vout)
/IN_BRAKE: BRD1.B3(6) (D4), J9.D24
/IN_BRAKE2: BRD1.B9(15) (D5), J9.D28
/IN_CAM1: BRD1.B10(14) (D1), J9.C5
/IN_CAM2: BRD1.B1(8) (D2), J9.C2
/IN_CLT: BRD1.C20(16) (AT3(CLT)), J9.C24
/IN_CLUTCH: BRD1.B11(13) (D6), J9.D23
/IN_CRANK: BRD1.B2(7) (D3), J9.C8
/IN_IAT: BRD1.C30(29) (AT2(IAT)), J9.C22
/IN_KNOCK1: BRD1.C34(25) (KNOCK1), J9.C29
/IN_KNOCK2: BRD1.C35(24) (KNOCK2), J9.C31
/IN_MAF: BRD1.C16(20) (AV7), J9.C1
/IN_MAP: BRD1.C13(23) (AV1(MAP)), C4.2, R6.1, U2.1 (VOUT)
/IN_OILT: BRD1.C19(17) (AT1), J9.C27
/IN_PPS1: BRD1.C25(34) (AV4), J9.D8
/IN_PPS2: BRD1.C15(21) (AV5), J9.D13
/IN_TPS1: BRD1.C24(35) (AV2(TPS)), J9.C19
/IN_TPS2: BRD1.C14(22) (AV3), J9.C10
/OUT_ETB1: BRD1.B7(2) (ETB1+), J9.C43
/OUT_ETB2: BRD1.B6(3) (ETB1-), J9.C44
/OUT_FUEL_PUMP_RELAY: BRD1.A8(5) (LS9(INJ9)), J9.D10
/OUT_IDLE_CLOSE: BRD1.A12(1) (LS15(FAN)), J9.C46
/OUT_IDLE_OPEN: BRD1.A23(13) (LS16(FUEL)), J9.C47
/OUT_IGN1: F3.2, Q1.2 (C), R10.2
/OUT_IGN2: F4.2, Q2.2 (C), R11.2
/OUT_IGN3: F5.2, Q3.2 (C), R12.2
/OUT_IGN4: F6.2, Q4.2 (C), R13.2
/OUT_IGN5: F7.2, Q5.2 (C), R14.2
/OUT_IGN6: F8.2, Q6.2 (C), R15.2
/OUT_INJ1: BRD1.A3(10) (LS1(INJ1)), J9.C33
/OUT_INJ2: BRD1.A15(21) (LS2(INJ2)), J9.C34
/OUT_INJ3: BRD1.A4(9) (LS3(INJ3)), J9.C35
/OUT_INJ4: BRD1.A16(20) (LS4(INJ4)), J9.C36
/OUT_INJ5: BRD1.A5(8) (LS5(INJ5)), J9.C37
/OUT_INJ6: BRD1.A6(7) (LS6(INJ6)), J9.C38
/OUT_INJ_RELAY: BRD1.A7(6) (LS7(INJ7)), J9.A1
/OUT_INTAKE_VALVE: BRD1.A10(3) (LS13(MAIN)), D4.2 (A), J9.C49
/OUT_MAIN_RELAY: BRD1.A19(17) (LS8(INJ8)), J9.B23
/OUT_MAP_THERMOSTAT: BRD1.A21(15) (LS12(INJ12)), D3.2 (A), J9.C45
/OUT_SEC_AIR_PUMP_RELAY: J9.D3, Q7.2 (D)
/OUT_SEC_AIR_PUMP_VALVE: BRD1.A11(2) (LS14), D5.2 (A), J9.C52
/OUT_VANOS_EXHAUST: BRD1.A9(4) (LS11(INJ11)), D2.2 (A), J9.C41
/OUT_VANOS_INTAKE: BRD1.A20(16) (LS10(INJ10)), D1.2 (A), J9.C40
/SEC_AIR_PUMP_RELAY: BRD1.A25(34) (IGN12), Q7.1 (IN), R16.2
/WBO_H-: J10.7, J10.8, J12.7, J12.8, M3.E5 (LSU_H+)
/WBO_Ip: J10.5, J12.5, M3.E3 (LSU_Ip)
/WBO_R_Trim: J10.6, J12.6, M3.E4 (LSU_Rtrim)
/WBO_Vs: J10.3, J12.3, M3.E1 (LSU_Un)
/WBO_Vs/Ip: J10.4, J12.4, M3.E2 (LSU_Vm)
GND: BRD1.A17(19) (GND), BRD1.A18(18) (GND), BRD1.A24(35) (GND), BRD1.B14(10) (GND), BRD1.B19(20) (GND), BRD1.B20(19) (GND), BRD1.C1(12) (GND_SENS), BRD1.C2(11) (GND_SENS), BRD1.C3(10) (GND_SENS), BRD1.C4(9) (GND_SENS), BRD1.C5(8) (GND_SENS), BRD1.C6(7) (GND_SENS), BRD1.C7(6) (GND_SENS), BRD1.C8(5) (GND_SENS), BRD1.C23(13) (GND_SENS), BRD1.C29(30) (GND_SENS), C1.1, C2.1, C3.1, C4.1, G6.1, G6.2, G6.3, G6.4, G6.5, J3.3, J7.1, J9.A4, J9.A5, J9.A6, J9.B20, J9.B21, J9.B22, J9.B24, J9.C15, J9.C17, J9.C18, J9.C20, J9.C21, J9.C23, J9.C25, J9.C28, J9.C30, J9.C32, J9.C48, J9.D7, J9.D12, J9.E5, J10.9, J10.10, J12.9, J12.10, M2.E1 (GND), M3.E6 (LSU_H-), M3.G (GND), Q1.3 (E), Q2.3 (E), Q3.3 (E), Q4.3 (E), Q5.3 (E), Q6.3 (E), Q7.3 (S), R1.2, R5.2, R6.2, R16.1, U1.3 (GND), U2.2 (GND)
unnamed: BRD1.A1(12) (HS2), P65.1
unnamed: BRD1.A2(11) (HS1), P64.1
unnamed: BRD1.A13(23) (HS3), P66.1
unnamed: BRD1.A14(22) (HS4), P67.1
unnamed: BRD1.A26(33) (IGN11), P71.1
unnamed: BRD1.A28(31) (IGN9), P70.1
unnamed: BRD1.A29(30) (IGN8), P69.1
unnamed: BRD1.A30(29) (IGN7), P68.1
unnamed: BRD1.B4(5) (VR2+), P74.1
unnamed: BRD1.B5(4) (VR1+), P72.1
unnamed: BRD1.B8(1) (ETB2-), P77.1
unnamed: BRD1.B12(12) (VR2-), P75.1
unnamed: BRD1.B13(11) (VR1-), P73.1
unnamed: BRD1.B15(9) (ETB2+), P76.1
unnamed: BRD1.C17(19) (AV9), P79.1
unnamed: BRD1.C18(18) (AV11), P81.1
unnamed: BRD1.C10(3) (5V_2), BRD1.C22(14) (5V_2), BRD1.C33(26) (5V_2), P83.1
unnamed: BRD1.C27(32) (AV8), P78.1
unnamed: BRD1.C28(31) (AV10), P80.1
unnamed: BRD1.C31(28) (AT4), P82.1
unnamed: F1.1, J9.A8
unnamed: F2.1, J9.D26
unnamed: G2.1, G2.6, G2.11
unnamed: G2.5, G2.10, G2.15
unnamed: G2.2, G2.7, G2.12
unnamed: G2.3, G2.8, G2.13
unnamed: G2.4, G2.9, G2.14
unnamed: G3.1, G3.6, G3.11
unnamed: G3.5, G3.10, G3.15
unnamed: G3.2, G3.7, G3.12
unnamed: G3.3, G3.8, G3.13
unnamed: G3.4, G3.9, G3.14
unnamed: G4.1, G4.6, G4.11
unnamed: G4.5, G4.10, G4.15
unnamed: G4.2, G4.7, G4.12
unnamed: G4.3, G4.8, G4.13
unnamed: G4.4, G4.9, G4.14
unnamed: G5.1, G5.6, G5.11
unnamed: G5.5, G5.10, G5.15
unnamed: G5.2, G5.7, G5.12
unnamed: G5.3, G5.8, G5.13
unnamed: G5.4, G5.9, G5.14
unnamed: G7.1, G7.6, G7.11
unnamed: G7.5, G7.10, G7.15
unnamed: G7.2, G7.7, G7.12
unnamed: G7.3, G7.8, G7.13
unnamed: G7.4, G7.9, G7.14
unnamed: G8.1, G8.6, G8.11
unnamed: G8.5, G8.10, G8.15
unnamed: G8.2, G8.7, G8.12
unnamed: G8.3, G8.8, G8.13
unnamed: G8.4, G8.9, G8.14
unnamed: J3.1, M3.W8 (V33_OUT)
unnamed: J3.2, M3.W7 (SWCLK)
unnamed: J3.4, M3.W6 (SWDIO)
unnamed: J3.5, M3.W5 (nReset)
unnamed: J9.A2, P1.1
unnamed: J9.A3, P2.1
unnamed: J9.A7, P3.1
unnamed: J9.A9, P4.1
unnamed: J9.B1, P5.1
unnamed: J9.B2, P6.1
unnamed: J9.B5, P7.1
unnamed: J9.B6, P8.1
unnamed: J9.B7, P9.1
unnamed: J9.B8, P10.1
unnamed: J9.B9, P11.1
unnamed: J9.B10, P12.1
unnamed: J9.B11, P13.1
unnamed: J9.B12, P14.1
unnamed: J9.B13, P15.1
unnamed: J9.B14, P16.1
unnamed: J9.B15, P17.1
unnamed: J9.B16, P18.1
unnamed: J9.B17, P19.1
unnamed: J9.B18, P20.1
unnamed: J9.B19, P21.1
unnamed: J9.C3, P22.1
unnamed: J9.C4, P23.1
unnamed: J9.C6, P24.1
unnamed: J9.C9, P25.1
unnamed: J9.C11, P26.1
unnamed: J9.C12, P27.1
unnamed: J9.C13, P28.1
unnamed: J9.C14, P29.1
unnamed: J9.C16, P30.1
unnamed: J9.C26, P31.1
unnamed: J9.C39, P32.1
unnamed: J9.C42, P33.1
unnamed: J9.C50, P34.1
unnamed: J9.C51, P35.1
unnamed: J9.D1, P36.1
unnamed: J9.D2, P37.1
unnamed: J9.D4, P38.1
unnamed: J9.D5, P39.1
unnamed: J9.D6, P40.1
unnamed: J9.D11, P41.1
unnamed: J9.D15, P42.1
unnamed: J9.D16, P43.1
unnamed: J9.D17, P44.1
unnamed: J9.D18, P45.1
unnamed: J9.D19, P46.1
unnamed: J9.D20, P47.1
unnamed: J9.D21, P48.1
unnamed: J9.D22, P49.1
unnamed: J9.D25, P50.1
unnamed: J9.D27, P51.1
unnamed: J9.D29, P52.1
unnamed: J9.D30, P53.1
unnamed: J9.D31, P54.1
unnamed: J9.D32, P55.1
unnamed: J9.D33, P56.1
unnamed: J9.D34, P57.1
unnamed: J9.D35, P58.1
unnamed: J9.D38, R1.1
unnamed: J9.D39, P59.1
unnamed: J9.D40, P60.1
unnamed: J9.E4, P62.1
unnamed: J9.E8, P61.1
unnamed: M2.V2 (CAN_VIO), M3.W2 (CAN_VIO)
unnamed: M2.V5 (CAN_TX), M3.W4 (CAN_TX)
unnamed: M2.V6 (CAN_RX), M3.W3 (CAN_RX)
unnamed: M3.J1 (SEL1), M3.J_GND1 (PULL_DOWN1)
unnamed: BRD1.A27(32) (IGN10), P63.1
unnamed: Q1.1 (G), R2.1
unnamed: Q2.1 (G), R3.1
unnamed: Q3.1 (G), R4.1
unnamed: Q4.1 (G), R7.1
unnamed: Q5.1 (G), R8.1
unnamed: Q6.1 (G), R9.1

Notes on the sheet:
Connectors 776228-1 776231-1 776231-2 Mating plugs 770680-1 776164-1 776164-2 Terminals 770854-1 all of the above cheap from ttiinc.com
For MPXH6400
TODO: Add "baro" silkscreen

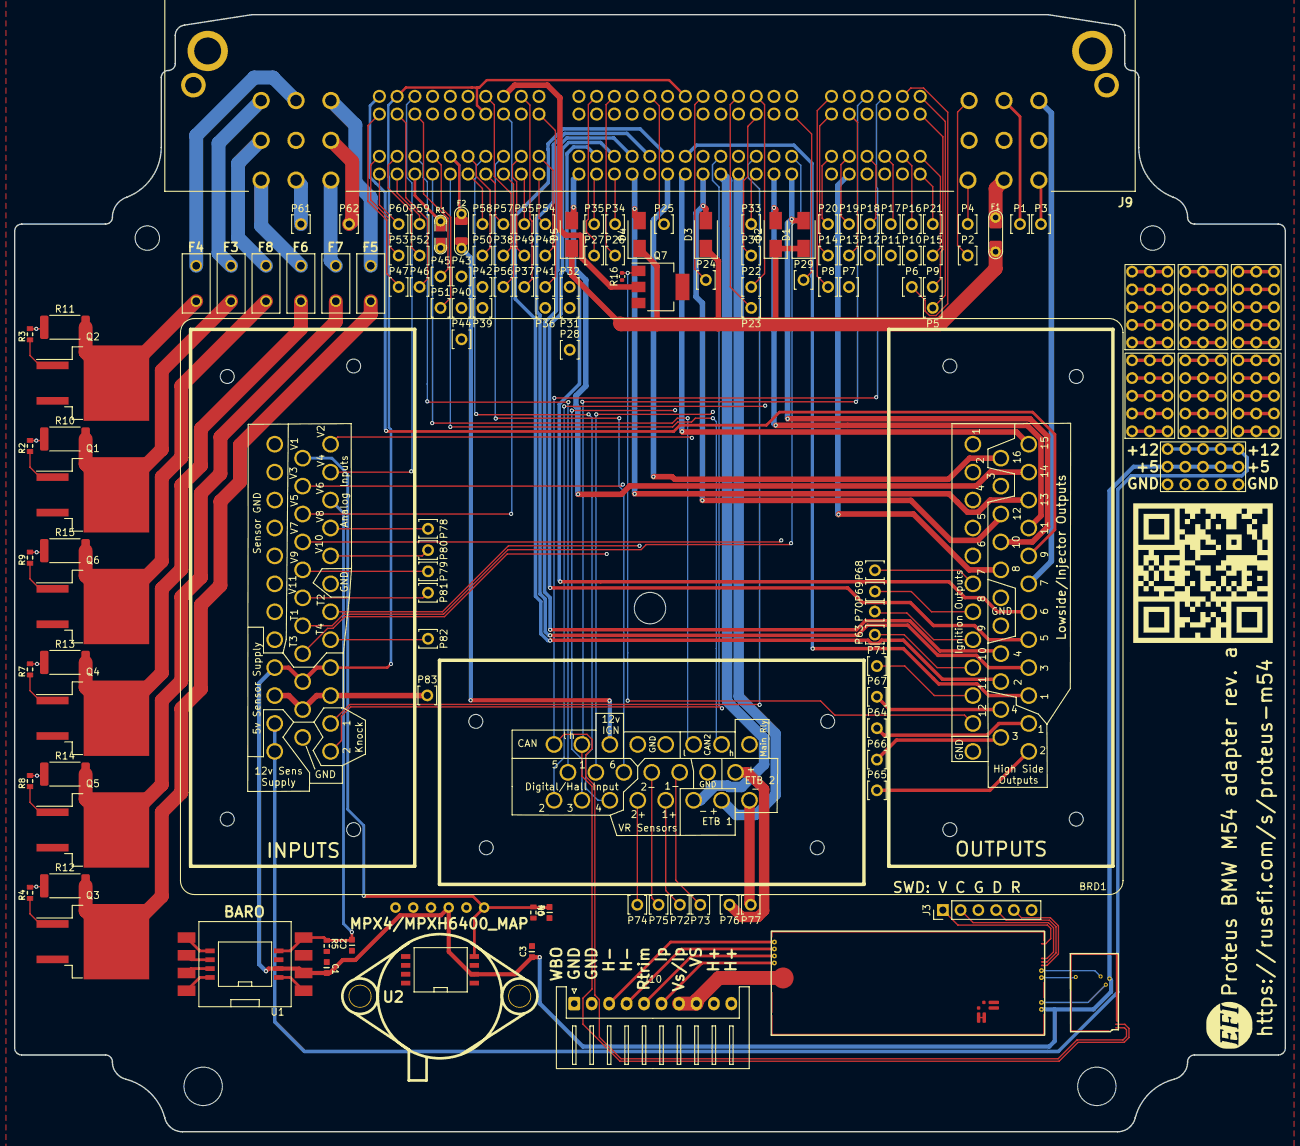
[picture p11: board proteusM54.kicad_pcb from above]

Board: 4 copper layers, 182.0 x 160.0 mm, 145 parts (1 on the bottom side), 200 nets.

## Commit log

2021-11-10 Upd sch, pcb
    [proteusM54.kicad_pcb, proteusM54.kicad_sch]
2021-11-13 Upd pcb
    [proteusM54.kicad_pcb, proteusM54.kicad_sch]
2021-11-13 Fab preview
    [M54-BOM.csv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]
